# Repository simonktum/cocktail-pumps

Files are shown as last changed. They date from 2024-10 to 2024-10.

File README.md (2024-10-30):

# cocktail-pumps

# Demo

[demo as mp4](https://github.com/user-attachments/assets/370c607c-63c9-449f-bd99-f4d8ec2cead2)

# Description

This project was developed in the context of the Cocktailmixer robot built by the Information Systems and Business Process Management chair at TUM. It builds upon earlier work by [Dominik Voigt](https://github.com/DominikVoigt/esp32-weightsensor) and Quirin Sailer.

The stated goal of this project was to implement a coherent system of weight cells and pumps which can be instructed by the [CPEE](https://arxiv.org/pdf/2208.12214) to mix various cocktails. This is achieved by utilizing 1 weight cell for the glass and 5 weight cells for each liquid which can then be pumped into the glass. The CPEE has access to individual weights and commands and can thus coordinate the asynchronous pumping, the fill level of the glass, the fill level of the liquids, etc with other processes of the cocktail robot.

# Setup

This is a quick introduction of how to get the current setup up and running. If you want more information on how to create this project, have a look at the [implementation](https://github.com/simonktum/cocktail-pumps/?tab=readme-ov-file#implementation).

0. Don't place anything on the weightcells yet
1. Connect the relays to power via a usb-c cable.
2. When the led lights up in red, press the button several times until the 15V mode is selected and the led lights in cyan. See [troubleshooting](https://github.com/simonktum/cocktail-pumps/?tab=readme-ov-file#troubleshooting) if it flashes or behaves otherwise.
3. Connect the pump esp by connecting it via a micro usb cable
4. If the esp for the weight cells was unplugged, remove the 5V and ground connections off the board and then plug the micro usb in to boot it. After around 7 seconds you can plug the 5V and ground connections back in.
5. Make sure the the aggregator script is running. You can test it by sending an http request to ``/pumps/weights``. Both esps should now be accessible to the CPEE via the aggregator  and ready to receive instructions.
6. Set the empty fill level by placing an empty bottle and sending a post to ``weights/<sensor-id>/empty``. Likewise, place a full bottle send a post request to ``weights/<sensor-id>/full`` to set the full weight. That allows you to receive the fill level with ``weights/<sensor-id>/level``.

## Limitations

There are some limitations in the current design:

- The esp for the loadcells occasionally reboots due to a [brownout](https://arduino.stackexchange.com/questions/76690/esp32-brownout-detector-was-triggered-upon-wifi-begin#76692) flag
- The wiring and inconsistent behavior of the ESP can be finicky (see [troubleshooting](https://github.com/simonktum/cocktail-pumps/?tab=readme-ov-file#troubleshooting))
- The loadcells can loosen over time because they are screwed directly into the 3d printed part

# Implementation

It the final implementation this project combines in total 6 load cells and 5 pumps. The materials for them are [here](/weightsensors/README.md) and [here](/pumps/ReadMe.md). The project also contains the CAD Files for all 3D printed parts which you can find [here](/docs/3D%20Prints/).

## CPEE Intetegration

<p align="center">
CPEE Graph
</p>

The CPEE implementation can be found [here](/docs/CPEE/Cocktail_Pumps.xml).

The process starts by requesting the fill level of the bottle place on the second weight cell. This is done thought a GET request to ``/weights/sensor_1113/level`` If the resulting fill level is larger than 10% a command is sent to the aggregator to fill the glass from pump 1 by 20 grams. The endpoint is a POST to ``/pumps/fill/1/20`` The aggregator script uses the ``CPEE-CALLBACK`` header to perform the filling filling of the glass asynchronous. The callback is sent once the glass is filled by the requested amount (in grams).

## Architecture

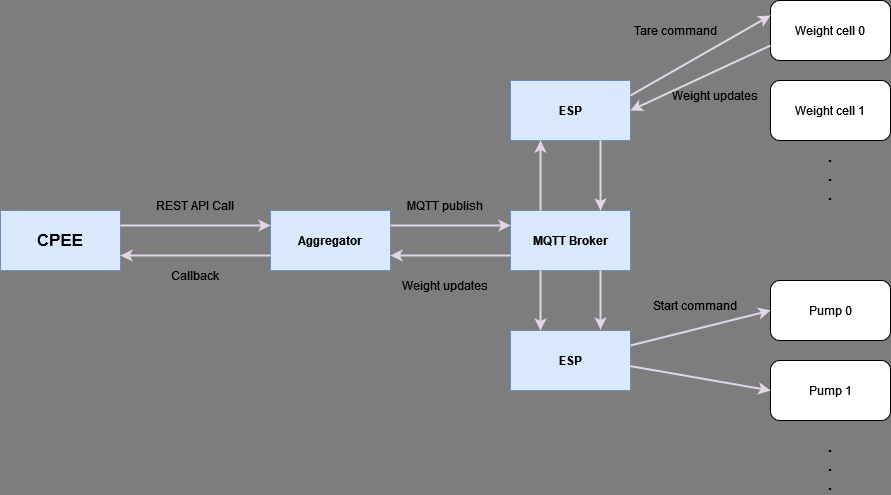
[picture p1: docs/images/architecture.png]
CPEE Graph


The esp controlling the weightsensors and the esp controlling the pumps are both sending and receiving instructions over the same MQTT Broker. The subscribed topics are ``cocktail/weight/+`` and ``cocktail/pumpen/``. The CPEE does not send MQTT instructions directly, instead it interfaces with an aggregator. This aggregator listens to updates on the MQTT topics and forwards instructions by the CPEE in the same topic channels. The aggregator provides a REST API to the CPEE which provides information about the current status of the sensors and possible instructions. It also holds the latest weight measured by each weight cell.

The documentation for the endpoints is in their respective sections below.

## Aggregator

The aggregator is a flask application found in ``weightsensors/src/aggregator``. It facilitates the communication between the ESPs and the CPEE. The specific endpoints are mentioned in the respective sections. There also two deployment scripts you might find useful.

- A the startup script for the aggregator found in ``weightsensors/src/aggregator``
- A simple moscitto MQTT broker in ``weightsensors/src/scripts``

## Weightsensors

The code is running on a [ESP-32 Dev Kit C V4](https://cdn.shopify.com/s/files/1/1509/1638/files/AZ282_A_19-2_DE_B08BTS62L7.pdf?v=1719330230) board and uses a HX711 Analog-To-Digital Converted (ADC) with the [olkal/HX711_ADC](https://github.com/olkal/HX711_ADC) implementation. The sensor measurements are sent via MQTT to an MQTT Broker and then aggregated and made available via a REST API by another MQTT Client (Python Paho/Flask).

The software of the weight cell is split up into two main components, the deploy code which runs the main program, and the calibrate code which can be used to find the calibration values. The sensor code is in the `weightsensors/src` directory. The aggregator code is in the `weightsensors/aggregator` subdirectory.
Like Dominik, I compiled the sensor code using PlatformIO which can be installed as a VS Code Extension.

Before the weight cell can be deployed using the `deploy.cpp` file, a couple of things have to be adapted in it.
If you manually noted down the factor, set `useEEPROM` to `false` and update the `calibrationValue` variable accordingly. If you saved it to EEPROM just set the `useEEPROM` to `true`. To connect to the WiFi, set the WiFi's `ssid` and `password` to the corresponding variables.
Lastly, to allow communication with the MQTT Broker you have to set the port (`port` variable) and IP Address (`server` variable) of the Mosquitto MQTT Broker. Note that if you use the `startupBroker` bash script in the `scripts` subdirectory, the port has to be equal to the `listener` entry in the `mosquitto.conf` file.

For more information, please look at Dominik's original Readme which can be found [here](https://github.com/DominikVoigt/esp32-weightsensor?tab=readme-ov-file).

### Wiring

<p align="center">
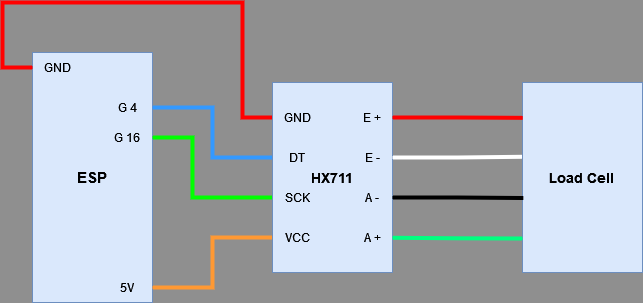
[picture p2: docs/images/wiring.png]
Wiring Diagram

</p>

While the color coding of the weight cell wires was consistent with the image, they can differ. To identify the pairs the most reliable way is to measure the resistance of each pair of wires (make sure to measure within the correct range to see the resistance values). Each of the correct pairs of wires should have a resistance of about 1000 Ohm and the other (wrong) pair combinations around 750-850 Ohm.

This is the wiring setup of a single weight cell. All cells follow this schema and are connected to the following pins:

- Cell 0 with DT = 4 and SCK = 16
- Cell 1 with DT = 2 and SCK = 15
- Cell 2 with DT = 5 and SCK = 17
- Cell 3 with DT = 19 and SCK = 18
- Cell 4 with DT = 32 and SCK = 33
- Cell 5 with DT = 12 and SCK = 14

<br>
<p align="center">
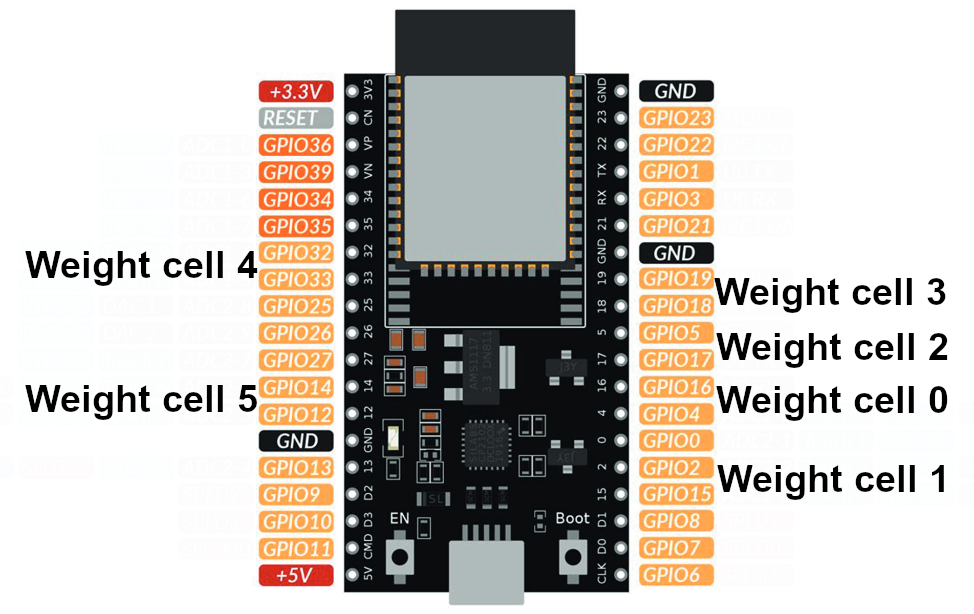
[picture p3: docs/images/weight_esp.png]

</p>

### Calibration

Each load cell has to be calibrated with a calibration value which has to be found empirically. This can be done by selecting the `calibrate.cpp` in the `platformio.ini` file and then using the "Upload and Monitor" task to run the calibration program. When following the program either note the calibration factor down or save it to EEPROM.

### Aggregator Endpoints

- weights: Data of all sensors that data was aggregated on
- weights/\<sensor-id\>: Data of a particular sensor specified by the <sensor-id> can be seen under the name property of the weight endpoint
- weights/\<sensor-id\>/name: Name of the sensor, corresponds with \<sensor-id\>
- weights/\<sensor-id\>/weight: Latest published weight of the sensor
- weights/\<sensor-id\>/full: Weight of the completely filled container on the scale. Null if weight not set previously via a POST to this endpoint
- weights/\<sensor-id\>/empty: Weight of the completely empty container on the scale. Null if weight not set previously via a POST to this endpoint
- weights/\<sensor-id\>/level: Current fill level based on the weight of the container on the scale, requires full and empty to be set via the corresponding endpoints
- cocktail/weight/: Tares all weight cells to set the new zero point

The ESP listens to the following MQTT instruction:

- `TARE` Tares all weight cells to set the new zero point

The weightsensors can also output their readings to an OLED Display which was implemented by Dominik. However it is not used in this implementation.

### 3D Printed parts

You can find all STL files [here](/docs/3D%20Prints/).

<p align="center">
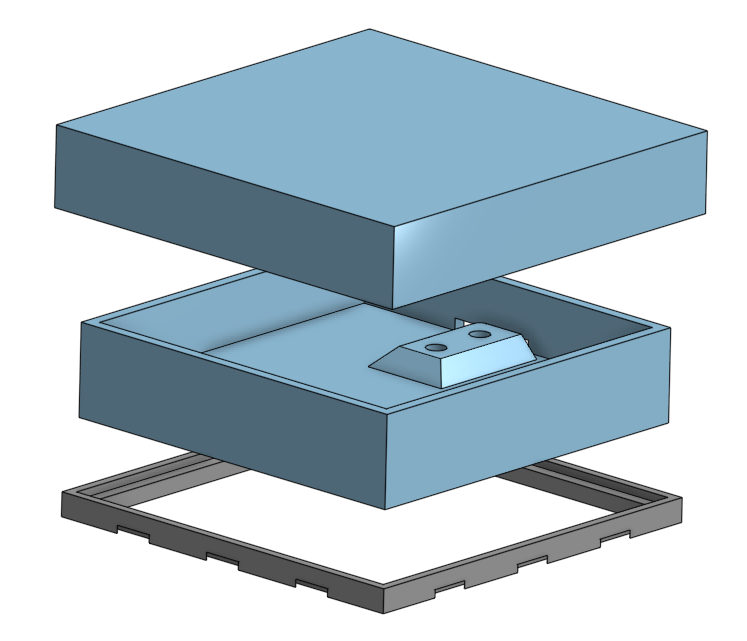
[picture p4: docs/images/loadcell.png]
Case for the load cells

</p>

The case for the load cell is an improved designed based on Dominik's original case. It is reduced to the 3 essential pieces:

1. A top cover to keep out water splashes. It needs to be installed onto the weight cell first.
2. A bottom cover which includes a slightly larger cable hole.
3. A bracket to hold the cell in place and connect it to other ones with dovetails

<p align="center">
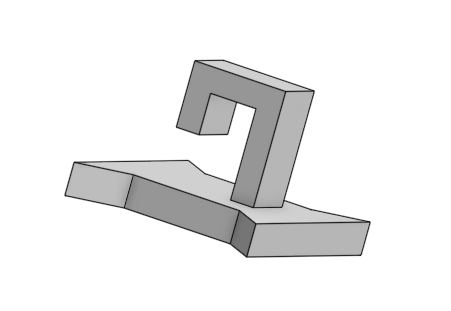
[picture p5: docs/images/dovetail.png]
Dovetail connectors

</p>

The dovetail connector includes a bracket to hold small cables.

<p align="center">
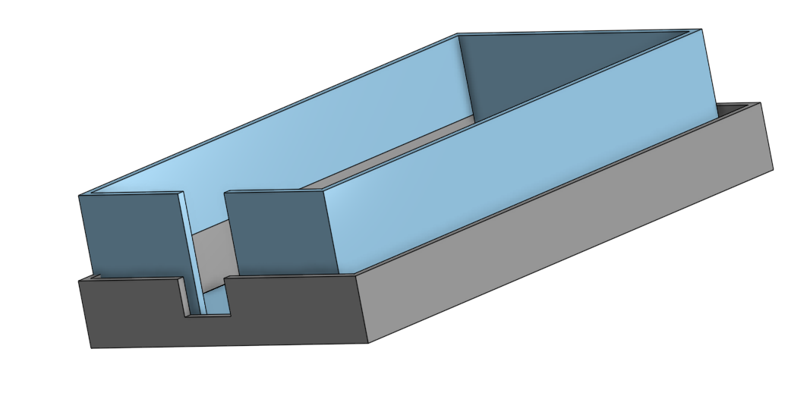
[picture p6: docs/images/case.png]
Case for the ESP and converters

</p>

The basic case houses the ESP and converters to save them from water splashes.

## Pumps

The pumps are controlled by a separate ESP, which controls up to 8 relays to drive them. The ESP receives the various commands over MQTT from the aggregator on the topic ``cocktail/pumpen``.

Like the the sensor esp code, you first need to set the correct wifi details and MQTT Broker address. All MQTT instructions can reference multiple pumps by including multiple numbers e.g. ``ON023-``. The trailing dash ensures no additional pumps are incorrectly identified.

The ESP listens to the following MQTT instructions:

- `ON12-` turns on relay 1 and 2 
- `OFF12-` turns off relay 1 and 2
- `BURST01-` turns on relay 0 for the fixed time of 1 sec
- `TIMED0AS2-` turns on relay 0 for the specified time in seconds, here 2 sec

The power to drive the relays is provided by a ZY12PDN board with the following [color indicators](https://github.com/manuelbl/zy12pdn-oss#usage-instructions):  

| Color  | Fixed Voltage |
| :----- | :-- |
| Red | 5V  |
| Yellow | 9V  |
| Green  | 12V |
| Cyan | 15V |
| Blue | 20V |
| Purple | Configure fixed voltage mode with highest available voltage. |

The pumps can be driven with 15V or 20V, though I would recommend 15V since that is what I tested them with.

The remaining hardware was not implemented by me. Please check the original [Readme](/pumps/ReadMe.md) by Quirin Sailer for more information.

### Aggregator Endpoints

- /pumps/\<string:pump\>/burst: Run the specified pump for 1 second.
- /pumps/\<string:pump\>/timed/\<int:time\> Run the specified pump for a given amount of time in seconds.
- /pumps/fill/\<string:pump\>/\<int:amount\> Asynchronously fills the glass from the specified pump up to the amount specified in grams. Note: The script first checks if a weight is detected on sensor 0, i.e. the glass and will run the pump for a maximum of 10 times and otherwise abort.

### 3D Printed parts

Since the pumps were already developed, only the tube fixture was 3d printed by me and is provided here. You can find all STL files [here](/docs/3D%20Prints/).

<p align="center">
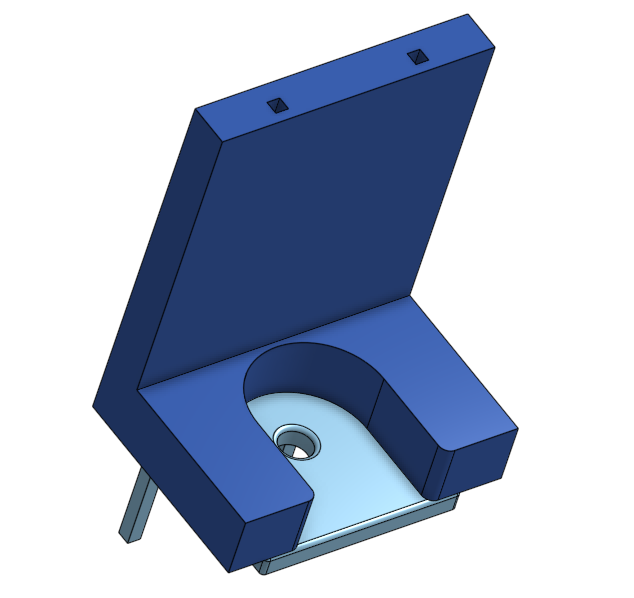
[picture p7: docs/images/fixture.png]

</p>

The current, less than optimal, fixture for the tubes.

<p align="center">
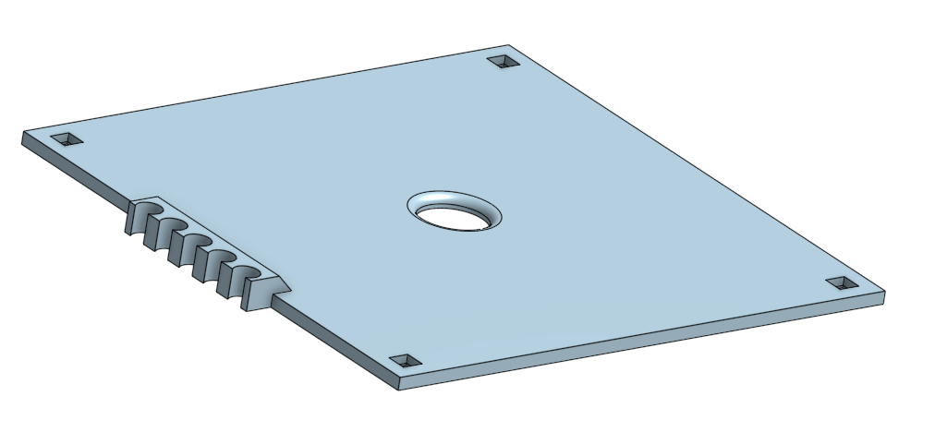
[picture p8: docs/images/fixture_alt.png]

</p>

This is an alternative plate with the correct dimensions to hold up to 5 tubes with a diameter of 6 mm.

# Troubleshooting

To make this project easily reproducible here are some common issues I ran into:

## Weightsensors

- When flashing the esp fails because ``the wrong boot mode is detected`` you need to put it into download mode by pressing and holding the boot button on the board for 1-2 sec.
However this might still fail on the loadcell esp, in which case also disconnect 5V power and ground cables during boot and wait until the loadcells were initialized after the reboot.
- Similarly, if you encounter the error ``A fatal error occurred: Serial data stream stopped: Possible serial noise or corruption.``, disconnect the 5V power and ground connections.
- The mqtt message might look weird in some clients because of the byte order
- If the zero point of the loadcell is set incorrectly, you need to send a tare command by pressing t in the serial monitor
- The zero point might change unexpectedly if the weightcell esp experiences a brownout and reboots

## Pumps
- The power delivery for the pump relays is picky about the rotation of the usb-c cable. It the led does not illuminate, turn it by 180° and try again.
- The power delivery requires a 5V input first and then you can cycle through the power profiles by pressing the button
- If the power delivery led flashes you are either in configuration mode, or your input is unsuitable

You can use the following resources for troubleshooting the power delivery
- https://github.com/manuelbl/zy12pdn-oss
- https://www.alexwhittemore.com/notes-on-usb-pd-triggers-and-zy12pdn-instructions/
- https://goughlui.com/2021/08/31/quick-review-yzx-studio-zy12pdn-usb-c-pd-decoy-board/

## CPEE
- If the CPEE process is stopped because if encountered an HTTP response outside of 200-300, ensure that the aggregator script is running and does so on the correct port and endpoint

# Credits

The original weightcell implementation was done by [Dominik Voigt](https://github.com/DominikVoigt/esp32-weightsensor) and the pump system by Quirin Sailer.

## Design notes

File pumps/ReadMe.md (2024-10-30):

Below is a copy of the original readme by Quirin Sailer

----

# Relay Ansteuerung
Das Hauptziel dieses Projekts ist die Erstellung eines Systems, das das unabhängige Ansteuern von bis zu acht Relays über das MQTT-Protokoll ermöglicht.

Jedes dieser Relays kann dann genutzt werden, um verschiedene Lasten, wie beispielsweise Pumpen, zu steuern. Die Steuerung der Relays erfolgt durch den ESP32 Mikrocontroller, der MQTT-Nachrichten von einem MQTT-Broker empfängt.

Jede Nachricht gibt an, welches Relay (identifiziert durch eine Nummer zwischen 0 und 7) aktiviert oder deaktiviert werden soll. Die Nachrichten werden über das MQTT-Topic "/cmnd/Relay/Status" gesendet.

## Kickstart Bedienungsanleitung
Eine kurze Anleitung:
1. Prüfen, dass alle Anbauten, wie Pumpen korrekt verkabelt sind
2. Prüfen dass die Konfiguration des ESPs korret ist ([siehe Anpassungen](#anpassungen))
3. Spannungsversorgung herstellen ([siehe Energieversorgnung](#energieversorgung))
4. MQTT Nachrichten an ESP senden ([siehe Konzept](#konzept))

## Anpassungen
In dem gegebenen Code können verschiedene Anpassungen vorgenommen werden, um ihn auf spezifische Anforderungen zuzuschneiden. Hier sind einige der Bereiche, in denen Anpassungen möglich sind:

- **WiFi-Konfiguration:** Die Konstanten für die SSID und das Passwort des WiFi-Netzwerks, mit dem sich der ESP32 verbinden soll, können am Anfang des Codes angepasst werden. Diese Konstanten definieren den Namen und das Passwort des Netzwerks, das der ESP32 zum Verbinden verwenden soll.

- **MQTT-Konfiguration:** Ebenfalls am Anfang des Codes können die Konstanten für den MQTT-Server, den Port und das Topic angepasst werden. Diese Konstanten definieren, wo sich der MQTT-Broker befindet (der Server und der Port) und welches Topic der ESP32 abonnieren und auf das er hören soll.

- **Pin-Konfiguration:** Die genutzten Pins des ESP32 können angepasst werden. Es ist wichtig zu beachten, dass nur die digitalen GPIO-Pins des ESP32 verwendet werden können. Diese Pins haben eine D-Nummer, die im Pinout des ESP32 angegeben ist.

Es ist zu beachten, dass die D-Nummern im Code anders nummeriert sind als im Pinout. Zum Beispiel ist D1 im Code Pin Nummer 5 und D2 ist Pin Nummer 4. Deshalb ist es wichtig, das Pinout des ESP32 zu konsultieren, wenn Sie die Pin-Konfiguration im Code ändern. (https://i0.wp.com/randomnerdtutorials.com/wp-content/uploads/2018/08/ESP32-DOIT-DEVKIT-V1-Board-Pinout-36-GPIOs-updated.jpg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)

Das Flashen des ESPs erfolgt mittels der Arduino IDE. Tutorials hierfür finden sich im Internet z.b. https://randomnerdtutorials.com/getting-started-with-esp32/

## Konzept

In diesem Szenario agiert ein ESP32 als ein MQTT-Client, der sich mit einem spezifizierten WLAN verbindet und auf ein bestimmtes MQTT-Topic, nämlich "/cmnd/Relay/Status", lauscht. Der ESP32 wird über dieses Topic gesteuert, was bedeutet, dass Befehle oder Aktionen, die durch den ESP32 ausgeführt werden sollen, an dieses Topic gesendet werden.

Die Aktionen, die der ESP32 ausführt, werden durch den Payload des MQTT-Nachrichten bestimmt. Wenn der Payload das Wort `ON` enthält, gefolgt von einer Zahl zwischen 0 und 7, aktiviert der ESP32 das entsprechende Relay. Diese Relays sind durchnummeriert und entsprechen den im Payload angegebenen Zahlen. Analog dazu, wenn der Payload das Wort `OFF` enthält, deaktiviert der ESP32 das entsprechende Relay. Beispielsweise kann mit der Message `ON14` das Relay 1 und 4 angeschaltet werden, während `OFF034` Die Relays 0,3 und 4 ausschaltet

Zusätzlich verfügt der ESP32 über einen seriellen Ausgang, der zur Protokollierung von Informationen verwendet wird. Diese Protokollierung erfolgt bei einer Baudrate von 9600.

## Aufbau

### Aufbau der Hardware
#### Verwendete Komponenten
Die Hauptkomponenten dieses Projekts sind:

 - Ein ESP32 Mikrocontroller (5)
 - Ein 8-Kanal-Relays-Modul (4)
 - Bis zu 8 Pumpen
 - Ein Gehäuse, das den ESP32 und das Relays-Modul beherbergt
 - Ein USB-C Input (2)
 - Ein Micro USB Input (1)
 - Ein Breadboard
 - Eine USB-C PD Platine (3)
 - Verschiedene Kabel und Stecker

#### ESP32 und Gehäuse

Der ESP32 ist das Herzstück dieses Projekts. Er ist zusammen mit allen anderen Komponenten (außer der Pumpen) in dem Gehäuse eingebaut.

#### Energieversorgung
Das Gehäuse hat 2 Eingänge, ein Micro USB und ein USB-C Anschluss.
Über den Micro USB Anschluss (1) wird die Betriebsspannung für den ESP32 bereitgestellt. Außerdem kann über diesen Anschluss der ESP32 programmiert werden. Desweiteren werden die Relays mit den 5V angesteuert.

Über den USB-C Anschluss (2) wird per Power Delivery (PD) die Betriebsspannung für die Pumpen bzw. Anbaugeräte bereitgestellt.
Die Pumpen sind für eine Einsatzspannung von 12V ausgelegt, längere Tests haben aber ergeben, dass ein Einsatz bei 20V allerdings ebenfalls bedenkenlos durchgeführt werden können.
Um den Aufbau des Systems zu vereinfachen haben wir uns dazu entschieden die Stromversorgung mittels [Power Delivery](https://de.wikipedia.org/wiki/Universal_Serial_Bus#Energieversorgung) zu realisieren, da so der Bedarf an einen externen Labornetzteil wegfällt.

Leider ist die verwendete Platine, welche USB-C Power Delivery bereistellt nicht optimal geeignet. So startet die Platine mit einer Leistung von nur 5V. Um die Spannung zu erhöhen, muss der Deckel des Gehäuses geöffnet werden und der Button auf der Platine 3 mal gedrückt werden. Eine kleine LED auf der Platine zeigt die Spannung an:
- Rot 5V
- Grün 9V
- Grün? 15V
- Hellblau 20V

Für die Pumpen kann sowohl 15V, als auch 20V verwendet werden. Power Delivery ist für maximal 100W ausgelegt, was mehr als ausreichend ist.

Theoretisch wäre es möglich den ESP32 auch mittels den Power Delivery des USB-C Anschlusses zu befeuern, allerdings wäre dann ein Step Down Converter nötig, welcher die Spannung von 20V auf 5V reduziert, desweiteren haben Motoren relativ hohe Anlaufströme, welche die Funktionsfähigkeit des ESPs beeinträchtigen könnten. Das Programmieren des ESPs könnte man per Over-the-Air Update (OTA) durchführen und hätte damit auch keinen Bedarf an einen physischen Micro USB. Allerdings kann das OTA Update erfahrungsgemäß auch fehlschlagen, was ein Ausbau des ESPs erfordern würde. Aus diesen Gründen haben wir uns dafür entschieden den ESP über ein eigenen Anschluss anzusteuern.

LED bei 5V
*LED bei 5V*
LED bei 9V
*LED bei 9V*
LED bei 15V
*LED bei 15V*
LED bei 20V
*LED bei 20V*

#### Breadboard und Relays-Modul

Im Inneren des Gehäuses ist der ESP32 auf einem Breadboard aufgesteckt, das zwei Spannungsleitungen hat:

- Die obere Leitung führt 5V für das Relays-Modul (6)
- Die untere Leitung führt 20V für die Pumpen (7)

Das 8-Kanal-Relays-Modul ist so verdrahtet, dass es Masse schaltet. Dies ermöglicht den Einsatz von Spannungen bis zu 50V. Falls zusätzliche Spannung benötigt wird, kann diese einfach hinzugefügt werden, indem die Masse der zusätzlichen Spannung mit der 20V-Masse verbunden wird. Das Masse-Schalten verhindert jedoch die Verwendung eines Schutzleiters, daher ist die maximale Spannung auf 50V begrenzt [Rechtlicher Hinweis](https://www.bgetem.de/arbeitssicherheit-gesundheitsschutz/themen-von-a-z-1/elektrische-gefaehrdungen-1/elektrotechnische-arbeiten-qualifikation/arbeiten-an-elektrisc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).

#### GPIO und Pumpen

Der ESP32 steuert das 8-Kanal-Relays-Modul über seine GPIOs an. Der 20V Input ist auf mehrere Stecker aufgeteilt, um eine Überlastung einer einzelnen Leitung zu verhindern und mögliche Wärmeentwicklung entgegenzuwirken.

Der genaue Aufbau ist im Folgenden dargestellt:

Schematischer Aufbau

Blick ins Ghäuse

Bitte beachten, dass die korrekte Verschaltung der Komponenten für das ordnungsgemäße Funktionieren des Systems unerlässlich ist. Es ist wichtig, das korrekte Pinout und die spezifischen Anforderungen der verwendeten Hardwarekomponenten zu beachten.

### Ausgänge
Das Gehäuse besitzt insgesamt 16 Ausgänge, wobei immer 2 ein paar ergeben. Am Gehäuse findet sich ander Vorderseite die Nummerierung der einzelnen Ausgänge und deren Poralität. Zu beachten ist, dass nur die Masse markiert ist.

Gehäuse von außen

### Aufbau des Codes
**1. Konstanten und Variable:**
Der nächste Abschnitt definiert einige Konstanten für den WiFi-Zugriff und den MQTT-Server sowie die Pins, an die die Geräte angeschlossen sind. Es wird ein AsyncMqttClient-Objekt namens mqttClient erstellt.

**2. WiFi und MQTT Verbindung:**
Es werden Funktionen definiert, um eine Verbindung zum WiFi (connectToWifi()) und zum MQTT Server (connectToMqtt()) herzustellen.

**3. WiFi Ereignisse:**
Die Funktion WiFiEvent behandelt zwei spezifische WiFi-Ereignisse: Wenn das Gerät eine IP-Adresse vom Router erhält (was bedeutet, dass es erfolgreich verbunden ist) und wenn das Gerät die Verbindung zum WiFi verliert.

**4. MQTT Ereignisse:**
In den Funktionen onMqttConnect und onMqttMessage wird definiert, was geschehen soll, wenn das Gerät eine Verbindung zum MQTT-Server herstellt bzw. wenn eine MQTT-Nachricht empfangen wird. In onMqttMessage wird auf bestimmte Inhalte in der empfangenen Nachricht geprüft, um die entsprechenden Aktionen auszuführen (in diesem Fall das Einschalten oder Ausschalten von Pins).

**5. Setup Funktion:**
In der Setup-Funktion werden die serielle Kommunikation initialisiert, die Pin-Modi festgelegt und Ereignishandler für WiFi- und MQTT-Ereignisse registriert. Zudem wird versucht, eine Verbindung zum WiFi herzustellen.

**6. Hauptschleife (Loop Funktion):**
Die Hauptschleife (loop()) ist in diesem Skript leer, da alle Aktionen durch Ereignishandler ausgelöst werden, die auf eingehende WiFi- oder MQTT-Ereignisse reagieren.

Bei Fragen gerne eine Email an:\
[pumpenmann@sailer.software](pumpenmann@sailer.software)

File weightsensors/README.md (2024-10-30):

Below is a copy of the original readme by Dominik Voigt

----

# Esp32-Weightsensor

## Demo

Demo GIF of measurement

## Description

Load cells can provide very reliable weight-sensing data for a wide variety of industrial applications.

In the context of the Cocktailmixer robot built by the [Information Systems and Business Process Management](https://www.cs.cit.tum.de/bpm/chair/) chair at [TUM](https://www.tum.de/en/) there are a wide variety of applications for this such as presence sensing for a cocktail queue and the monitoring of fill level of different bottles used by the robot to mix cocktails.

Therefore goal of this project was to construct a proof of concept weight measurement cell using a 4-Wire Loadcell. The sensor measurement are read using a 24-bit ADC (HX711) by a Microcontroller (ESP-32) and sent via MQTT to an MQTT Broker (Mosquitto) and then aggregated and made available via a REST API by another MQTT Client (Python Paho/Flask).

## Features
This project allows deployment of an arbitrary number of weight measurement cells within the range of the configured WiFi and an aggregator that allows monitoring of the currently measured weight by each cell.

Additionally, it allows to monitor the fill level of a calibrated container placed on a load cell in percentage. For this the container has to be calibrated on the weight cell by measuring it in its weight when being full and when it is empty by invoking the corresponding `full` and `empty` POST endpoints in the REST API. 

For more details about the REST API capabilities see [here](#endpoints)

A small OLED Display provides on-site measurements for the connected weight cell.

The project also contains the CAD Files of the 3-D print casing for mounting the Load cell.

## Technical Section

### Bill of Material

- A 4-wire Load Cell - Note: In this case, a 3kg one was used but different cells have different dimensions and can thus require changes in the placement and dimensions of the mounting holes
- An HX711 Analog-To-Digital Converted (ADC)
- ESP-32 (WiFi capable)
- Breadboard
- 4 Male-Male Dupont Wires 
- 6 Female-Male Dupont Wires 
- OLED (128x64) Display that uses I2C Communication - note: Depending on the Display Driver (SH1106/SD1306) the object class for the `u8g2` object in the `deploy.cpp` might have to be adapted accordingly
- 3D Printer (For the Casing)
- Very Recommended ([Reason](#hardware-setup--wiring)): Male Dupont Pins and a corresponding Ratcheting Crimping tool 

### Hardware Setup & Wiring

Note that the Wires of the load cell are extremely thin and sensitive as they are stranded and not solid core wires and each stand is extremely thin. To make it easier to work with, crimp a Male Dupont Pin onto the end of each load cell wire.

Now it is important to check the configuration of the Load-Cell Wires. A 4-wire Load cell contains two pairs of wires. One pair should be connected to E+ and E- and the other to A+ and A-.
One pair is responsible for providing the current and the other for measuring the voltage over the [Wheatstone bridge](https://en.wikipedia.org/wiki/Wheatstone_bridge) that is created by the strain gauges on the load cell. Note that the order of the pairs does not matter as does the ordering of the two wires per pair (either wire of the first pair can be connected to E+ and the other one to E-).

To identify the pairs the most reliable way is to measure the resistance of each pair of wires (make sure to measure within the correct range to see the resistance values).
Each of the correct pairs of wires should have a resistance of about 1000 Ohm and the other (wrong) pair combinations around 750-850 Ohm.

In my case the wire pairs were black-red and white-green.
To make it easier I recommend to use a 4-pin Housing to hold all four Dupont pins of the wires together (put the wires of the pairs next to each other).

For the wiring follow this diagram (note that this corresponds to the case when the pairs are black-red and white-green (adapt this to your situation)):

Wiring Diagram

### Software Setup - Sensor

The software is split up into two main components. The sensor code is directly in the `src` directory. The aggregator code is in the `aggregator` subdirectory.
The simplest way to get the sensor code compiling and running is to use PlatformIO which can be installed as a VS Code Extension.

When PlatformIO is installed just open the command palette (`Ctrl + Shift + P` when using the  standard VS Code keyboard shortcuts) and run the "Upload" or "Upload and Monitor" PlatformIO task.
This automatically compiles the code and uploads it to the connected ESP-32.

In the `src` folder, there are two sensor code files, `calibrate.cpp` and `deploy.cpp`.
To decide which of the files to compile and upload to the ESP change the `build_src_filter` property in the `platformio.ini` file within the root folder.

First, each load cell has to be calibrated, for this, the calibration value has to be found empirically. This can be done by selecting the `calibrate.cpp` in the `platformio.ini` file and then using the "Upload and Monitor" task to run the calibration program. When following the program either note the calibration factor down or save it to EEPROM.

Before the weight cell can be deployed using the `deploy.cpp` file, a couple of things have to be adapted in it.
If you manually noted down the factor, set `useEEPROM` to `false` and update the `calibrationValue` variable accordingly. If you saved it to EEPROM just set the `useEEPROM` to `true`.

If you want to see a TUM logo display on startup set the `enableBootDisplay` variable to `true`.

To connect to the WiFi, set the WiFi's `ssid` and `password` to the corresponding variables.
Lastly, to allow communication with the MQTT Broker you have to set the port (`port` variable) and IP Address (`server` variable) of the Mosquitto MQTT Broker. Note that if you use the `startupBroker` bash script in the `scripts` subdirectory, the port has to be equal to the `listener` entry in the `mosquitto.conf` file.

### Software Setup - Aggregator

Similar to the sensor, the Mosquitto MQTT Broker IP Address and port also have to be configured in the `aggregator.py` to enable the aggregator to connect to it for this change the `ipAddressMQTT` and `portMQTT` variables respectively.
Note that the `aggregator.py` makes use of the Paho and Flask libraries. To ensure a working environment you can create an environment and then run `pip install -r requirements.txt` from the root of the project.

### Run

To run the aggregator it is advisable to use the premade `startupAggregator.sh` script as it runs the aggregator directly using the flask run command that is essential for the aggregator to work correctly.

The sensors can be started at an arbitrary moment in time, but have to connect to the MQTT broker during startup.
The aggregator has to be started after Mosquitto MQTT Broker.
Thus the `startupBroker.sh` script should be run first and subsequently the `startupAggregator.sh` script should be run from a shell with the correct Python environment active

### Employed Technologies

To make the weight measurement cells small and cheap an ESP-32 controller was used for the Microcontroller as it  comes with out-of-the-box WiFi capabilities and is quite cheap.

To send the data to an aggregator the MQTT protocol is used as it is the SOTA protocol for IOT applications.

The aggregator that collects the sensor data was written using Python and the Paho and Flask libraries.
The Paho library is used to enable the aggregator to communicate with the MQTT Broker by acting as an MQTT client and subscribing to the sensor data of all weight measurement cells.
The Flask library allows the aggregator to expose the data of the different sensors via a simple and light weight REST API. Furthermore, the REST API enables the [monitoring of fill levels](#features) of bottles on a per-cell-basis.

### Endpoints

- weights: Data of all sensors that data was aggregated on
- weights/\<sensor-id\>: Data of a particular sensor specified by the <sensor-id> can be seen under the name property of the weight endpoint
- weights/\<sensor-id\>/name: Name of the sensor, corresponds with \<sensor-id\>
- weights/\<sensor-id\>/weight: Latest published weight of the sensor
- weights/\<sensor-id\>/full: Weight of the completely filled container on the scale. Null if weight not set previously via a POST to this endpoint
- weights/\<sensor-id\>/empty: Weight of the completely empty container on the scale. Null if weight not set previously via a POST to this endpoint
- weights/\<sensor-id\>/level: Current fill level based on the weight of the container on the scale, requires full and empty to be set via the corresponding endpoints

### 3-D printed Casing

To mount the Load Cell to the Casing, first mount the second plate from the top to the load cell and then mount the bottom casing to the load cell through the holes in the bottom.

The top casing should just slide on and of the top mounting plate (that was mounted first). If this is not the case maybe some sanding of the edges of the top mounting plate may be required.

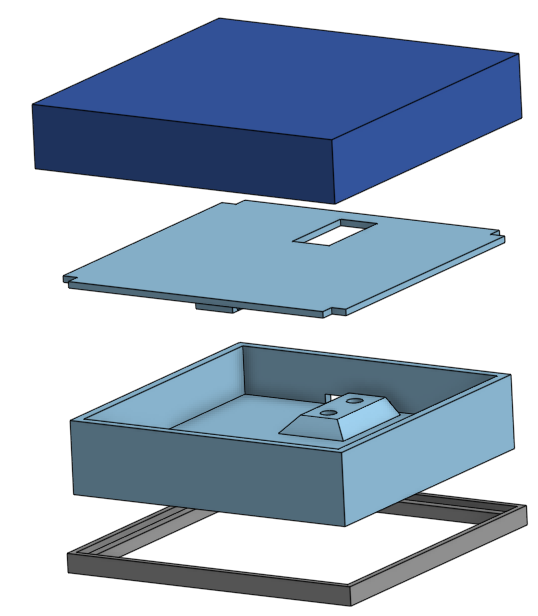
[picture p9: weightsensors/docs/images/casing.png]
Image of Model


### Credit

Code skeleton for weight measurements acquired from [here](https://github.com/olkal/HX711_ADC/blob/master/examples/Read_1x_load_cell_interrupt_driven/Read_1x_load_cell_interrupt_driven.ino)

WiFi and MQTT code skeleton acquired from [here](https://randomnerdtutorials.com/esp32-mqtt-publish-subscribe-arduino-ide/)

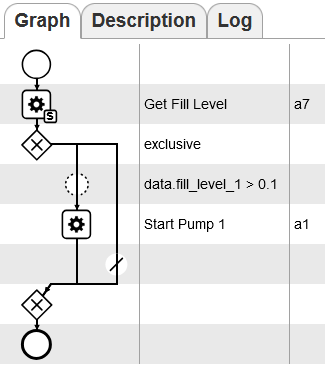
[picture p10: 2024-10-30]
docs/CPEE/graph.png

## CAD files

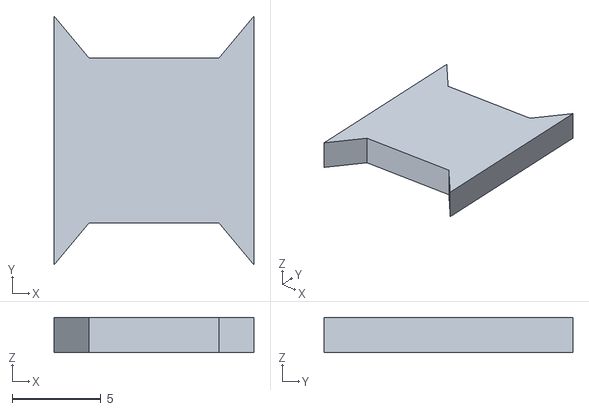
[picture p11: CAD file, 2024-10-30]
docs/3D Prints/Weightsensor - Dovetail.stl
11.3 x 14.1 x 2.00

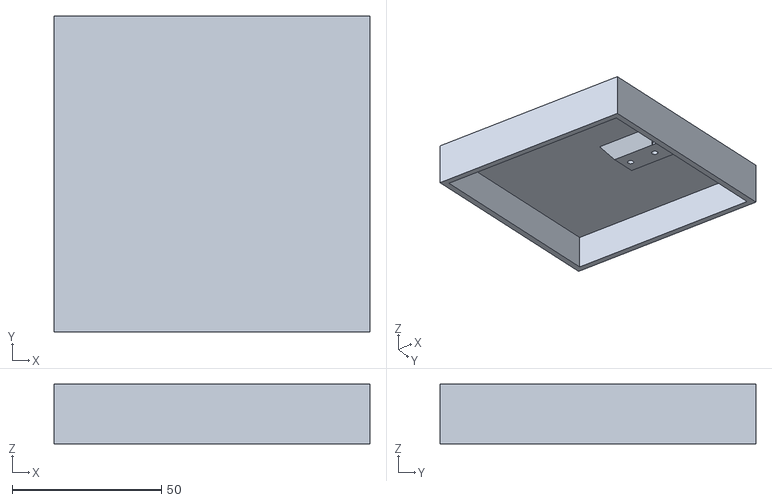
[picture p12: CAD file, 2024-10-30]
docs/3D Prints/Weightsensor - Top Mount Plate.stl
106.0 x 106.0 x 20.0

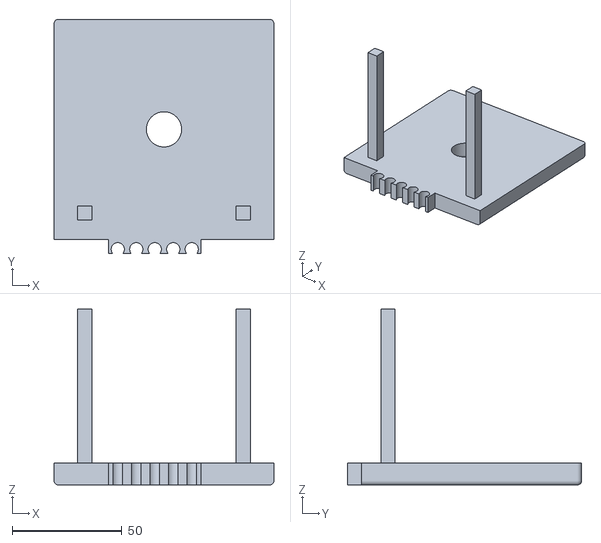
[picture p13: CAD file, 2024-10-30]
docs/3D Prints/Original Fixture - Top.stl
100.0 x 106.5 x 80.0

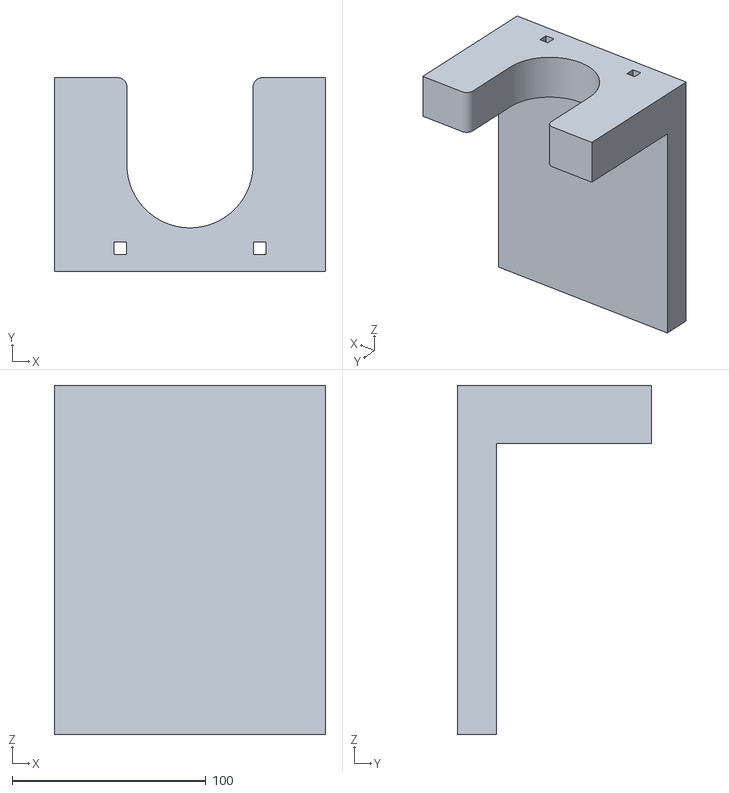
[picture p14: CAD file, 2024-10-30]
docs/3D Prints/Original Fixture - Bottom.stl
140.0 x 100.0 x 180.0

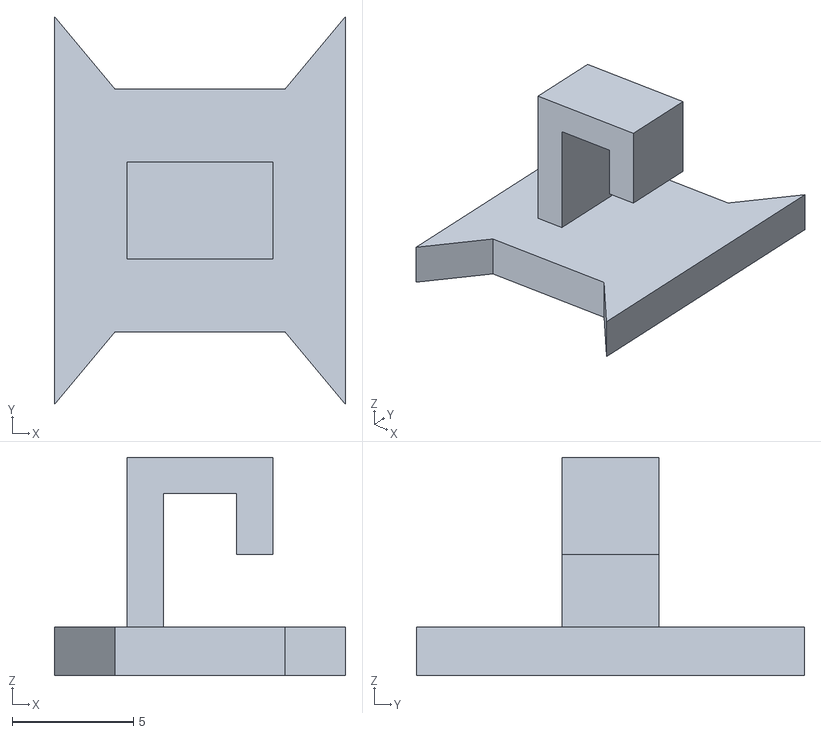
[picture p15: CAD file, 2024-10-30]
docs/3D Prints/Weightsensor - Dovetail with cableholders(1).stl
12.0 x 16.0 x 9.00

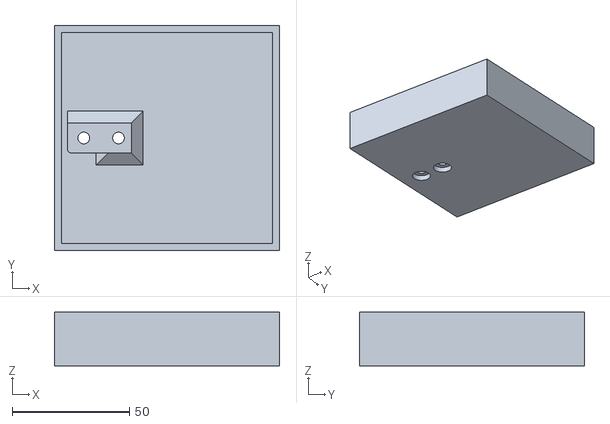
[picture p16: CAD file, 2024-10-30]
docs/3D Prints/Weightsensor - Bottom.stl
96.0 x 96.0 x 23.0

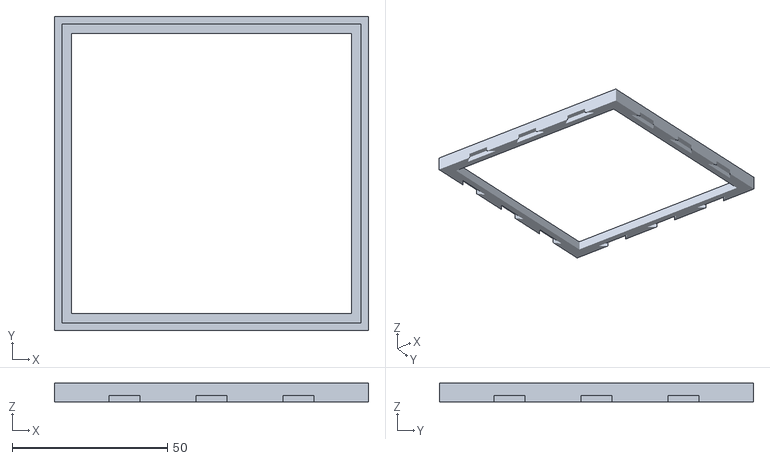
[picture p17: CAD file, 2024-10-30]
docs/3D Prints/Weightsensor - Bottom Offset.stl
101.0 x 101.0 x 6.00

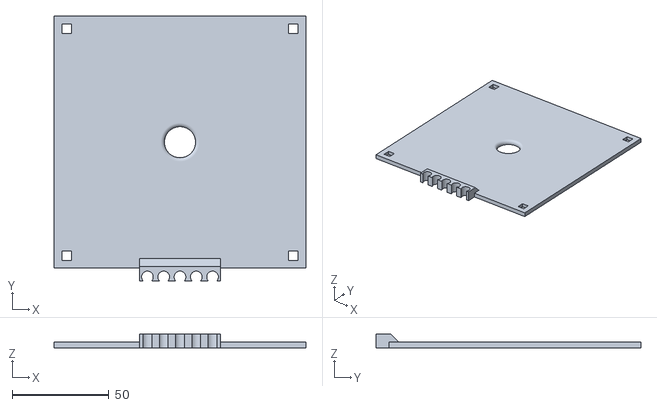
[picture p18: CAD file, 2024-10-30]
docs/3D Prints/Weightsensor - Fixture.stl
130.0 x 136.5 x 7.00

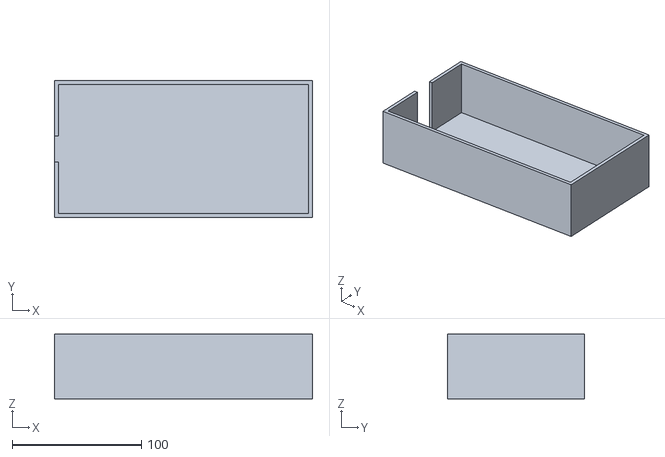
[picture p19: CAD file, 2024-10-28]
docs/3D Prints/Case_bottom.stl
200.0 x 106.0 x 50.0

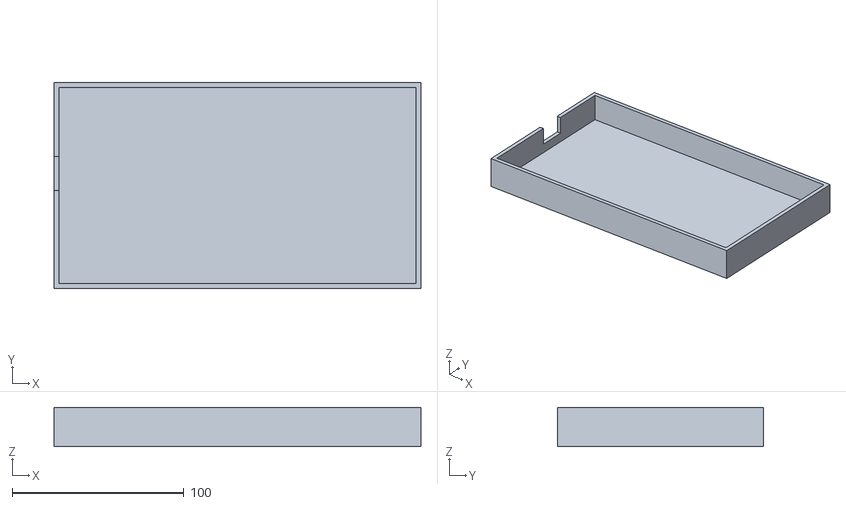
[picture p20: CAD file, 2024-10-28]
docs/3D Prints/Case_top.stl
214.0 x 120.0 x 23.0

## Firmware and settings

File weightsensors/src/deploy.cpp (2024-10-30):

/*
   Code skeleton for weight measurements acquired from:
      https://github.com/olkal/HX711_ADC/blob/master/examples/Read_1x_load_cell_interrupt_driven/Read_1x_load_cell_interrupt_driven.ino
   WiFi and MQTT code skeleton acquired from:
      https://randomnerdtutorials.com/esp32-mqtt-publish-subscribe-arduino-ide/

*/

#include <HX711_ADC.h>
#include <EEPROM.h>
#include <Wire.h>
#include <U8g2lib.h>
#include <string>
#include <WiFi.h>
#include <PubSubClient.h>

const int numer_of_loadcells = 6;

const int HX711_dout = 4; // microcontroller unit > HX711 dout pin, must be external interrupt capable!
const int HX711_sck = 16; // microcontroller unit > HX711 sck pin

// additional load cells
const int LC1_dout = 2;
const int LC1_sck = 15;

const int LC2_dout = 5;
const int LC2_sck = 17;

const int LC3_dout = 19;
const int LC3_sck = 18;

const int LC4_dout = 32;
const int LC4_sck = 33;

const int LC5_dout = 12;
const int LC5_sck = 14;

// HX711 constructor:
HX711_ADC LoadCell[numer_of_loadcells] = {HX711_ADC(HX711_dout, HX711_sck), HX711_ADC(LC1_dout, LC1_sck), HX711_ADC(LC2_dout, LC2_sck), HX711_ADC(LC3_dout, LC3_sck), HX711_ADC(LC4_dout, LC4_sck), HX711_ADC(LC5_dout, LC5_sck)};

float calibrationValue = 451.22;
float calibrationValueLC1 = 743.72;
float calibrationValueLC2 = 392.59;
float calibrationValueLC3 = -118.45;
float calibrationValueLC4 = 410.49;
const int calVal_eepromAdress = 0;
bool useEEPROM = false;
bool serviceEnabled = true;

unsigned long t = 0;
const int serialPrintInterval = 100;
volatile boolean newDataReady;

U8G2_SH1106_128X64_NONAME_F_HW_I2C u8g2(U8G2_R0, /* reset=*/U8X8_PIN_NONE);
bool enableBootDisplay = true;

// Replace the next variables with your SSID/Password combination
const char *ssid = "ssid";
const char *password = "password";

IPAddress server(1, 1, 1, 1);
const int port = 1;
const std::string sensorID[] = {"1111", "1112", "1113", "1114", "1115", "1116"};

// Weight displayed on the display
int displayedWeight[numer_of_loadcells] = {0, 0, 0, 0, 0, 0};
// Weight Measured in the previous iteration
int lastWeight[numer_of_loadcells] = {0, 0, 0, 0, 0, 0};
bool firstMeasurement[numer_of_loadcells] = {true, true, true, true, true, true};

WiFiClient espClient;
PubSubClient client(espClient);

void displaySensorIDBottom()
{
  u8g2.setCursor(30, 60);
  u8g2.setFont(u8g2_font_ncenB08_tr);
  u8g2.print("Sensor ID: ");
  u8g2.print(sensorID[0].c_str());
}

void displayReconnectMessage()
{
  u8g2.clearBuffer();
  u8g2.setFont(u8g2_font_ncenB08_tr);
  u8g2.setCursor(0, 15);
  u8g2.print("Disconnected");
  u8g2.setCursor(0, 40);
  u8g2.print("Reconnecting...");
  displaySensorIDBottom();
  u8g2.sendBuffer();
}

// interrupt routine:
void dataReadyISR()
{
  if (LoadCell[0].update() || LoadCell[1].update() || LoadCell[2].update() || LoadCell[3].update() || LoadCell[4].update() || LoadCell[5].update())
  {
    newDataReady = 1;
  }
}

void setupLoadcell()
{
  if (useEEPROM)
  {
    EEPROM.begin(512);
    EEPROM.get(calVal_eepromAdress, calibrationValue);
  }
  Serial.print("Using Calibration value:");
  Serial.println(calibrationValue);

  unsigned long stabilizingtime = 2000;
  boolean _tare = true;
  for (size_t i = 0; i < numer_of_loadcells; i++)
  {
    LoadCell[i].begin();
    LoadCell[i].start(stabilizingtime, _tare);
    if (LoadCell[i].getTareTimeoutFlag())
    {
      Serial.print("Timeout, check wiring to HX711 and pin designations for LoadCell ");
      Serial.println(i);
      while (true)
        ;
    }
    else
    {
      LoadCell[i].setCalFactor(calibrationValue);
      Serial.print("Startup for LoadCell ");
      Serial.print(i);
      Serial.println(" is complete");
    }
  }

  attachInterrupt(digitalPinToInterrupt(HX711_dout), dataReadyISR, FALLING);
  attachInterrupt(digitalPinToInterrupt(LC1_dout), dataReadyISR, FALLING);
  attachInterrupt(digitalPinToInterrupt(LC2_dout), dataReadyISR, FALLING);
  attachInterrupt(digitalPinToInterrupt(LC3_dout), dataReadyISR, FALLING);
  attachInterrupt(digitalPinToInterrupt(LC4_dout), dataReadyISR, FALLING);
  attachInterrupt(digitalPinToInterrupt(LC5_dout), dataReadyISR, FALLING);
}

void setupDisplay()
{
  u8g2.begin();
}

void setup_wifi()
{
  delay(10);
  // We start by connecting to a WiFi network
  Serial.println();
  Serial.print("Connecting to ");
  Serial.println(ssid);

  WiFi.begin(ssid, password);

  while (WiFi.status() != WL_CONNECTED)
  {
    delay(500);
    Serial.print(".");
  }

  Serial.println("");
  Serial.println("WiFi connected");
  Serial.println("IP address: ");
  Serial.println(WiFi.localIP());
}

void callback(char *topic, byte *message, unsigned int length)
{
  Serial.print("Message arrived on topic: ");
  Serial.print(topic);
  Serial.print(" Message: ");
  std::string messageTemp;

  for (int i = 0; i < length; i++)
  {
    Serial.print((char)message[i]);
    messageTemp += (char)message[i];
  }
  Serial.println();

  if (messageTemp.rfind("TARE", 0) == 0) // check if it starts with TARE
  {
    Serial.println("TARE command found");
    for (size_t i = 0; i < numer_of_loadcells; i++)
    {
      LoadCell[i].tareNoDelay();
      Serial.print("Completed tare for: ");
      Serial.println(i);
    }
  }
}

void setupMQTT()
{
  setup_wifi();
  client.setServer(server, port);
  client.setCallback(callback);
}

void displayBoot()
{
  u8g2.setCursor(20, 45);
  u8g2.setFont(u8g2_font_ncenB24_tr);
  u8g2.print("TUM");
  u8g2.sendBuffer();
  sleep(1);
}

void setup()
{
  Serial.begin(9600);
  delay(10);
  Serial.println();
  Serial.println("Starting...");

  setupLoadcell();
  setupDisplay();
  if (enableBootDisplay)
  {
    displayBoot();
  }
  if (serviceEnabled)
  {
    setupMQTT();
  }
}

void displayWeight(size_t i)
{
  u8g2.clearBuffer();
  u8g2.setFont(u8g2_font_ncenB10_tr);
  u8g2.setCursor(0, 15);
  u8g2.print("Current Weight of Load Cell");
  u8g2.print(i);
  u8g2.print(": ");
  u8g2.setCursor(0, 40);
  u8g2.print(displayedWeight[i]);
  u8g2.print(" grams");
  u8g2.println("");
  displaySensorIDBottom();
  u8g2.sendBuffer();
}

int gearState = 0;
void displayMeasuring()
{
  u8g2.clearBuffer();
  u8g2.setFont(u8g2_font_ncenB10_tr);
  u8g2.setCursor(0, 15);
  u8g2.print("Measuring");
  u8g2.setCursor(0, 40);
  u8g2.print("Weight  ");

  switch (gearState)
  {
  case 0:
    u8g2.print("/");
    break;
  case 1:
    u8g2.print("-");
    break;
  case 2:
    u8g2.print("\\");
    break;
  }
  gearState = ++gearState % 3;
  displaySensorIDBottom();
  u8g2.sendBuffer();
}

void publishWeightToMQTT(size_t i)
{
  std::string topic = "cocktail/weight/sensor_";
  topic = topic + sensorID[i];
  client.publish(topic.c_str(), reinterpret_cast<uint8_t *>(&displayedWeight[i]), sizeof(float));
}

void handleNewWeightData(size_t i)
{
  newDataReady = 0;
  // Cutoff milligrams as the weighing setup is not that precise
  int newWeight = static_cast<int>(LoadCell[i].getData());
  // The delta in weight is not large, do not update the display (could be due to noise)
  bool smallDelta = abs(newWeight - displayedWeight[i]) <= 5;
  // The delta in weight is pretty large and thus the weight measurement has not yet stabilized, do not update the display
  bool largeDelta = abs(newWeight - lastWeight[i]) >= 6;
  if (!firstMeasurement[i])
  {
    if (largeDelta && newWeight > 5)
    {
      displayMeasuring();
    }
    lastWeight[i] = newWeight;
    if (smallDelta || largeDelta || newWeight <= 5)
    {
      // Do not update the screen
      return;
    }
  }
  else
  {
    firstMeasurement[i] = false;
    lastWeight[i] = newWeight;
  }
  if (newWeight <= 5)
  {
    // for very small values or negative values just display 0 as the precision of the scale is not that great
    newWeight = 0;
  }
  displayedWeight[i] = newWeight;

  if (serviceEnabled)
  {
    publishWeightToMQTT(i);
  }
  displayWeight(i);
  Serial.print("Load_cell ");
  Serial.print(i);
  Serial.print(": ");
  Serial.print(newWeight);
  Serial.print(" grams");
  Serial.println("");
}

void reconnect()
{
  displayReconnectMessage();
  // Loop until we're reconnected
  while (!client.connected())
  {
    Serial.print("Attempting MQTT connection...");
    // Attempt to connect
    if (client.connect("ESP32Client"))
    {
      Serial.println("connected");
      std::__cxx11::string topic = "cocktail/weight/"; // topic for instructions
      const char *cstr = topic.c_str();
      boolean success = client.subscribe(topic.c_str());
      Serial.print("Subscribed to MQTT: ");
      Serial.println(success);
    }
    else
    {
      Serial.print("failed, rc=");
      Serial.print(client.state());
      Serial.println(" try again in 5 seconds");
      // Wait 5 seconds before retrying
      delay(5000);
    }
  }
}

void loop()
{
  if (serviceEnabled)
  {
    if (!client.connected())
    {
      reconnect();
    }
    client.loop();
  }
  // get smoothed value from the dataset:
  if (newDataReady)
  {
    if (millis() > t + serialPrintInterval)
    {
      for (size_t i = 0; i < numer_of_loadcells; i++)
      {
        handleNewWeightData(i);
      }
      t = millis();
    }
  }

  if (Serial.available() > 0)
  {
    char inByte = Serial.read();
    if (inByte == 't')
    {
      for (size_t i = 0; i < numer_of_loadcells; i++)
      {
        LoadCell[i].tareNoDelay();
      }
    }
  }

  if (LoadCell[0].getTareStatus())
  {
    Serial.println("Tare complete");
  }
}

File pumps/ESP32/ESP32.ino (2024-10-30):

#include <WiFi.h>
#include <WiFiClientSecure.h>
#include <AsyncMqtt_Generic.h>
#include <thread>
#include <chrono>
#include <iostream>
#include <sstream>

const char* ssid = "ssid";
const char* password = "password";
const char* mqttServer = "mqttServer";
const int mqttPort = 1;
const char* mqttTopic = "cocktail/pumpen";
const int pins[8] = { 27, 14, 26, 13, 33, 5, 18, 19 };

AsyncMqttClient mqttClient;

void connectToWifi() {
  Serial.println("Connecting to Wi-Fi...");
  WiFi.begin(ssid, password);
}

void connectToMqtt() {
  Serial.println("Connecting to MQTT...");
  mqttClient.connect();
}

void WiFiEvent(WiFiEvent_t event) {
  switch (event) {
    case ARDUINO_EVENT_WIFI_STA_GOT_IP:
      Serial.println("Connected to Wi-Fi. Connecting to MQTT...");
      connectToMqtt();
      break;
    case ARDUINO_EVENT_WIFI_AP_STADISCONNECTED:
      Serial.println("Disconnected from Wi-Fi. Reconnecting...");
      connectToWifi();
      break;
  }
}

void onMqttConnect(bool sessionPresent) {
  Serial.println("Connected to MQTT.");
  uint16_t packetIdSub = mqttClient.subscribe(mqttTopic, 2);
  Serial.print("Subscribing at QoS 2: ");
  Serial.println(mqttTopic);
  Serial.print("packetId: ");
  Serial.println(packetIdSub);
}

void setPinState(const char* payload, int state) {
  for (int i = 0; i < 8; i++) {
    char pinStr[2];
    itoa(i, pinStr, 10);
    if (strstr(payload, pinStr) != NULL) {
      Serial.print(i);
      Serial.println(state == HIGH ? " -- HIGH" : " -- LOW");
      digitalWrite(pins[i], state);
    }
  }
}

void activateInBurst(const char* payload, int state) {
  using namespace std::this_thread;
  using namespace std::chrono;
  setPinState(payload, LOW);
  sleep_for(milliseconds(1000));
  setPinState(payload, HIGH);
}

void activateWithTime(const char* payload, int time) {
  using namespace std::this_thread;
  using namespace std::chrono;
  int i = time * 1000;
  setPinState(payload, LOW);
  sleep_for(milliseconds(i));
  setPinState(payload, HIGH);
}

void onMqttMessage(char* topic, char* payload, AsyncMqttClientMessageProperties properties, size_t len, size_t index, size_t total) {
  //Inverted Relais!!!!!!
  Serial.print("Received: ");
  Serial.println(payload);
  String tmp = String(payload);
  tmp = tmp.substring(0, tmp.indexOf("-")+1); //need to cut of the stuff sent afterwards
  char const* instruction = tmp.c_str();
  Serial.print("Cut down String: ");
  Serial.println(instruction);
  if (strstr(instruction, "OFF") != NULL) {
    setPinState(instruction, HIGH);
  } else if (strstr(instruction, "ON") != NULL) {
    setPinState(instruction, LOW);
  } else if (strstr(instruction, "BURST") != NULL) {
    activateInBurst(instruction, LOW);
  } else if (strstr(instruction, "TIMED") != NULL) {
  tmp = String(instruction);
  String tmp_instructions = tmp.substring(0, tmp.indexOf("AS"));
  tmp = tmp.substring(tmp.indexOf("AS") + 2, tmp.indexOf("-"));
  char const* time = tmp.c_str();
  std::stringstream strValue;
  strValue << time;
  unsigned int intValue;
  strValue >> intValue;
  instruction = tmp_instructions.c_str();
    activateWithTime(instruction, intValue);
  }
}

void setup() {
  Serial.begin(9600);
  for (int i = 0; i < 8; i++) {
    pinMode(pins[i], OUTPUT);
  }
  for (int i = 0; i < 8; i++) {
    digitalWrite(pins[i], HIGH);
  }
  WiFi.onEvent(WiFiEvent);
  mqttClient.onConnect(onMqttConnect);
  mqttClient.onMessage(onMqttMessage);
  mqttClient.setServer(mqttServer, mqttPort);
  connectToWifi();
}

void loop() {
}
